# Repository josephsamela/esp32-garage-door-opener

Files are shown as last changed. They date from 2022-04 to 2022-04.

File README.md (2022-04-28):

# esp32-garage-door-opener

esp32 IoT device to open/close your garage door with Apple HomeKit

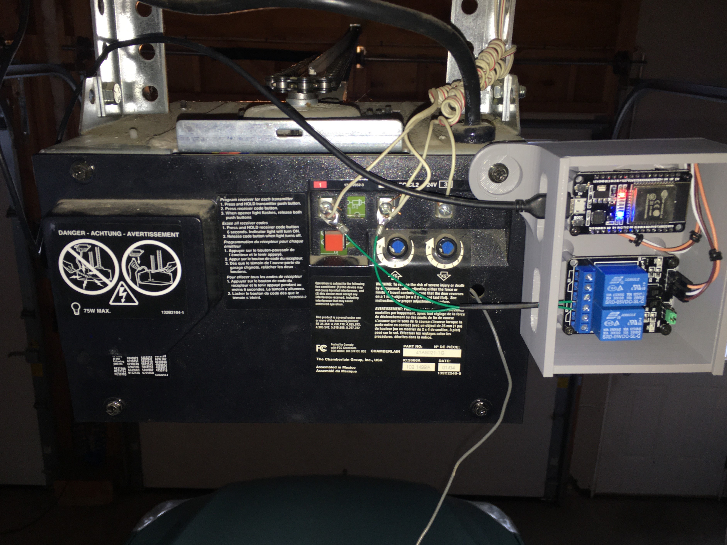
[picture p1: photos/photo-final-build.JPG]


## Software

This device can be controlled completely independent of any smart-home infastructure. It's simply an IoT "thing" you send HTTP GET requests to open/close your garage door.

That said, I personally am integrating this with Apple HomeKit. In order to do this you'll need a local instance of [Homebridge](https://homebridge.io/). You'll also need to install the [homebridge-http-garage](https://github.com/phenotypic/homebridge-http-garage) plugin for homebridge.

Once connected to your network, set a DHCP reservation so the device retains it's IP address. Then you can control it by sending HTTP requests to the routes below:

### Routes

The `/` endpoint is purely informational. It's helpful when setting up the garage door the first time.
```
/
```

The `/toggle` endpoint toggles the garage door. It's equivelant to you pushing the garage door button.

```
/toggle
```

The `status` endpoint will return json indicating the state of the garage door. `{"currentState":0}`
```
/status
```

The `setState` route accepts a query param called `value`. You can set state to `0` (open) or `1` (closed).
```
/setState?value=INT_VALUE
```

### Homebridge Configuration

I recommend following the default homebridge configuration suggested by the [homebridge-http-garage](https://github.com/phenotypic/homebridge-http-garage) plugin readme. Here's what I use:

```json
{
    "accessory": "GarageDoorOpener",
    "name": "Garage Door",
    "apiroute": "http://192.168.1.35",
    "openTime": 13,
    "closeTime": 13,
    "autoLock": false,
    "autoLockDelay": 20,
    "pollInterval": 120,
    "timeout": 2000,
    "http_method": "GET"
}
```

## Hardware

The hardware is an ESP32 microcontroller with a relay module. The rear of the garage door unit has three screw terminals connected to the wall switch.

The relay is connected between the two screw terminals connected to the garage door opener push-button. When the relay is closed the garage door unit recognizes this as a "button press" and opens/closes the door as if you pushed the button on the wall.

From the ESP32, I'm driving the relay board with `3.3V` and `GND` and using `D15` as the control pin set HIGH or LOW to control the relay. 

## Installation

Wire microcontroller to relay, and relay to garagedoor as shown.

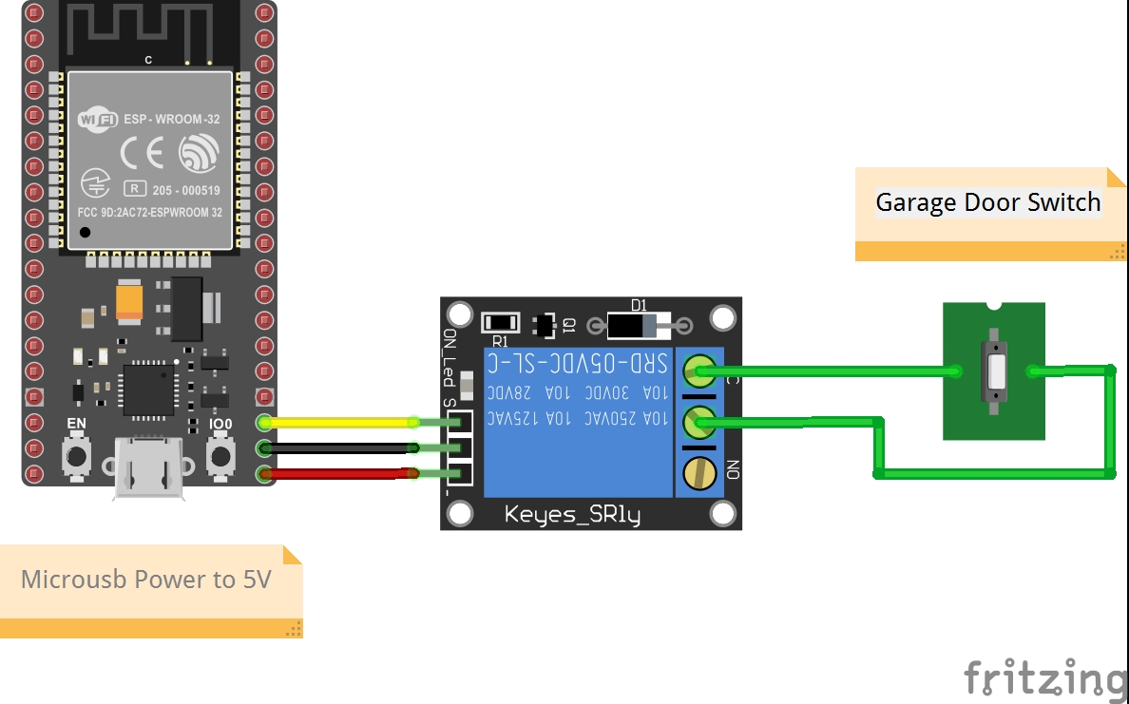
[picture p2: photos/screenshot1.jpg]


| ESP32 | Relay | Garage Door |
|:-----:|:-----:|:---:|
|  3.3V |  VCC  | |
|  GND  |  GND  | |
|  D15  | IN  | |
| | NC  | Switch 1  |
| | C | Switch 2  |

## Troubleshooting

*Does your sensor work initially, then become unresponsive?*

I had this issue after setting up my Homekit Hub (Apple TV). The sensor would become unresponsibe and require a restart ever couple hours. I found this was caused by the ESP32 WebServer library's default socket timeout. 

The HomeKit hub constantly polls the device to check it's status. Every time it does this, the HomeKit Hub (client) opens a socket connection to your device to request data. The WebServer will maintain that connection until the client closes the connection OR the connection times out. 

For some reason the sockets are not being closed and hang around until they timeout. Since the default timeout is long (2 seconds) all of these connections are being created faster then they're timing out and piling up until the server becomes unresponsive.

Here's how I fixed it. Find the `WebServer.h` header file. Located here on my computer.

```
C:\Users\<username>\AppData\Local\Arduino15\packages\esp32\hardware\esp32\2.0.2\libraries\WebServer\src\WebServer.h
```

Look for the line defining the `HTTP_MAX_CLOSE_WAIT` variable and change the default from `2000` to `100`.

```cpp
#define HTTP_MAX_CLOSE_WAIT 100 //ms to wait for the client to close the connection
```

Recompile and flash your firmware.

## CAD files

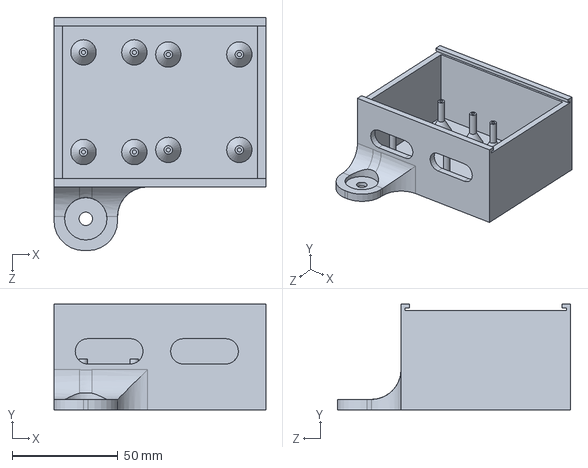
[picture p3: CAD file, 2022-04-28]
enclosure/device-enclosure.SLDPRT
100.0 x 50.0 x 110.0 mm

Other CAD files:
enclosure/device-enclosure.STL

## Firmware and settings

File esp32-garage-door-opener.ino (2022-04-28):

#include <WiFi.h>
#include <WiFiClient.h>
#include <WebServer.h>
#include <ESPmDNS.h>

const char* ssid = "<ENTER WIFI NAME HERE>";
const char* password = "<ENTER WIFI PASSWORD HERE>";

WebServer server(80);

const int led = 2;
const int relay = 15;
const int reset = 26;
const int resetInterval = 3600000; // 1hr by default
const int lockDuration = 14000; //default 14 second lockout

int requestedState = 1; // open=0, closed=1
int currentState = 1; // open=0, closed=1
int lockExpire = 0; 

void setup(void) {
  // Setup GPIO pin modes
  pinMode(led, OUTPUT);
  pinMode(relay, OUTPUT);
  pinMode(reset, OUTPUT);
  // Initialize GPIO positions
  digitalWrite(led, HIGH);
  digitalWrite(relay, HIGH);
  digitalWrite(reset, HIGH);
  
  Serial.begin(115200);

  // Connect to wifi
  WiFi.mode(WIFI_STA);
  WiFi.begin(ssid, password);
  WiFi.setSleep(false);
  
  // Wait for connection
  while (WiFi.status() != WL_CONNECTED) {
    delay(500);
    Serial.print(".");
  }
  Serial.print("Connected to ");
  Serial.println(ssid);
  Serial.print("IP address: ");
  Serial.println(WiFi.localIP());
  if (MDNS.begin("esp32")) {
    Serial.println("MDNS responder started");
  }

  server.on("/", []() {
    server.send(200, "text/plain", "This is Joe's Garage Door!\nSend a GET request to an endpoint below: \n\n`/toggle`\t\tToggle door state. Digital 'press' of the garage door button.\n`/reset`\t\tReset device. Remotely press reset button.\n`/status`\t\tGet JSON status of garage door.\n`/setState?value=1`\tSet state of garage door. Valid states are the two values, `open=0` and `closed=1`\n");
  });
  
  server.on("/toggle", []() {
    digitalWrite(led, LOW);
    toggleGarageDoorState();
    server.send(200, "text/plain", "Pressed garage door button. Door state will toggle.\n");
    digitalWrite(led, HIGH);
  });

  server.on("/reset", []() {
    server.send(200, "text/plain", "Resetting device. Please wait 10 seconds.\n");
    delay(100);
    digitalWrite(reset, LOW);
  });

  server.on("/status", []() {
    digitalWrite(led, LOW);
    server.send(200, "text/plain", "{\"currentState\":" + String(currentState) + ",\"requestedState\":" + String(requestedState) +"}\n");
    digitalWrite(led, HIGH);
  });

  server.on("/setState", []() {
    for (uint8_t i = 0; i < server.args(); i++) {
      if (server.argName(i) == "value" ) {
          requestedState = server.arg(i).toInt();
          server.send(200, "text/plain", "{\"currentState\":" + String(currentState) + ",\"requestedState\":" + String(requestedState) +"}\n");
        }
      }
  });

  server.onNotFound([]() {
    digitalWrite(led, 1);
    String message = "Route Not Found\n\n";
    message += "URI: ";
    message += server.uri();
    message += "\nMethod: ";
    message += (server.method() == HTTP_GET) ? "GET" : "POST";
    message += "\nArguments: ";
    message += server.args();
    message += "\n";
    for (uint8_t i = 0; i < server.args(); i++) {
      message += " " + server.argName(i) + ": " + server.arg(i) + "\n";
    }
    server.send(404, "text/plain", message);
  });

  server.begin();
  Serial.println("HTTP server started");
}

void toggleGarageDoorState() {
    digitalWrite(led, LOW);
    digitalWrite(relay, HIGH);
    delay(100);
    digitalWrite(relay, LOW);
    delay(100);
    digitalWrite(relay, HIGH);
    digitalWrite(led, HIGH);
}

void loop(void) {
  server.handleClient();

  if (requestedState != currentState) {
    if (millis() >= lockExpire) {
      toggleGarageDoorState();
      currentState = requestedState;
      lockExpire = millis() + lockDuration;
    }
  }

  if (millis() > resetInterval) {
    digitalWrite(reset, LOW);
  }
  
  delay(2);//allow the cpu to switch to other tasks
}
